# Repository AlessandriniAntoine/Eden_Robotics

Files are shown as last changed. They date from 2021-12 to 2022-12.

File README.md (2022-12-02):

# Eden_Robotics

Eden Robotics is a student project. The objective was to create a robotic arm capable of harvesting tomatoes. You can find a report [there](./Report/main.pdf).

<figure>
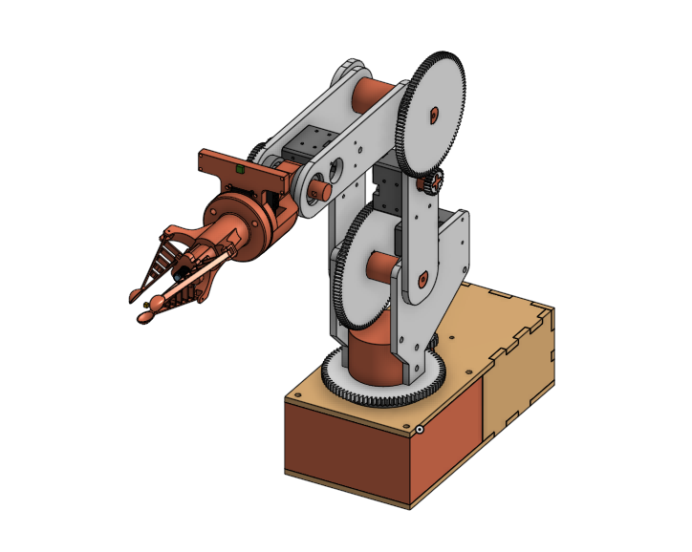
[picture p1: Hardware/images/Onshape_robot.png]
    
    <figcaption>Figure 1 : Robot Visualitaion</figcaption>
</figure>

<br/>
<br/>
<br/>

<figure>
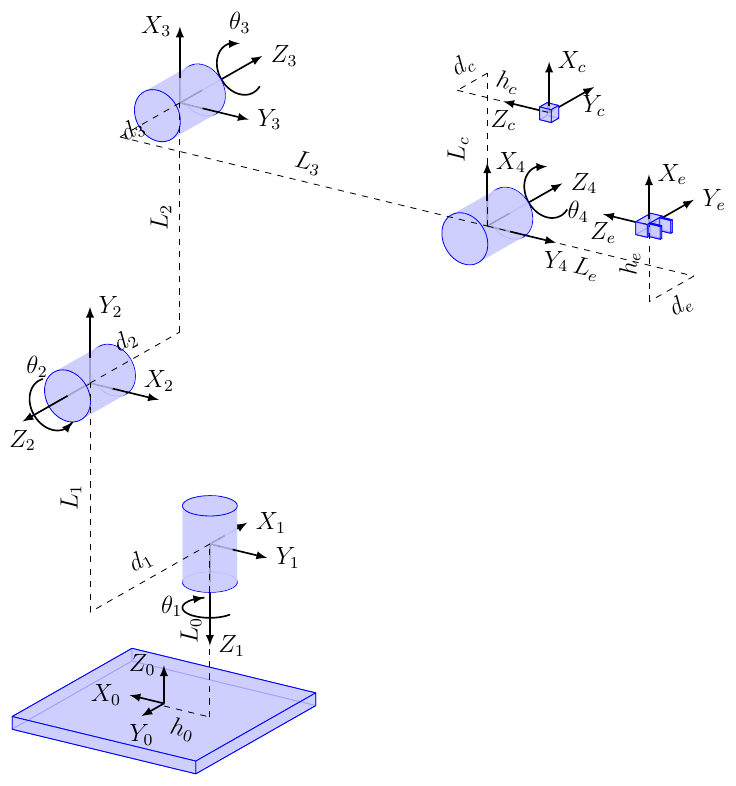
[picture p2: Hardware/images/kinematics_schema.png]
    
    <figcaption>Figure 2 : Kinematics schema</figcaption>
</figure>

## Hardware

We used the following hardware part :

- dynamixels motors and driver : U2D2, XL430,XC430, XM430,AX12W
- Raspberry pi 3
- USB camera

To construct the robot, the parts are in this [folder](./Hardware/stl). A notice can be found [there](./Hardware/Assembly_Plan.pdf). You can also found the Onshape model [here](https://cad.onshape.com/documents/8404446994fd5ae1242a5d56/w/0f8ef10f6026ba3e07bbdb54/e/7486e3cb0086b1a441d11061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).

We used Onshape to model the robot. Some rules, stated [here](./Hardware/README.md), must be respected during this creation. Thanks to this, a URDF model of the robot can be generated automatically (cf python part)

## Python

Each subfolder has a README file that explains more precisely how to use it.

### URDF

Using python, we transfer our Onshape model into an urdf model.

For more information see the [urdf_README](./Python/urdf/README.md).

### kinematics

Even if the inverse kinematics is done  in Matlab, some kinematics tools were done in python using modern_robotics library. Mainly because it facilitated the creation of node ROS and accelerated the process.

We used this library for :

- Forward kinematics
- compute configuration matrix of the end effector and the camera
- change point reference frame

For more information see the [kinematics_README](./Python/kinematics/README.md).

### Vision

Using openCV we have perfom :

- camera video display
- object tracking

For more information see the [vision_README](./Python/vision/README.md).

## Matlab

Thanks to the urdf file, it is possible to create a simscape multibody model of the robot.

Using matlab, we have perform:

- Forware kinematics
- Inverse kinematics
- closed loop model

For more information see the [matlab_README](./Matlab/README.md).

## Software

During the project, we used the following softwares :

- Matlab R2022a : ROS toolbox, Robotic system toolbox, simscape
- Python 3.8 : onshape-to-robot, modern robotics, openCV
- Ubuntu 20.04
- Onshape

## Useful links

- [eden_robotics_ros](https://github.com/AlessandriniAntoine/eden_robotics_ros.git) : branch ros1, package ros for this project
- [onshape-to-robot_documentation](https://onshape-to-robot.readthedocs.io/en/latest/)
- [modern_robotics_documentation](http://modernrobotics.org)
- [modern_robotics_github](https://github.com/NxRLab/ModernRobotics)

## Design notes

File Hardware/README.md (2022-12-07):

# Hardware

You can find the model here : [Onshape_model]([aa](https://cad.onshape.com/documents/8404446994fd5ae1242a5d56/w/0f8ef10f6026ba3e07bbdb54/e/7486e3cb0086b1a441d11061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)). You need an onshape acount to copy and modify it.

See the assembly instructions [here](./Assembly_Instructions.pdf)

## Design Rules

To keep a clean work environment, the following points should be respected:

- Name all parts with a specific name: it is the ID of the part and it has to be unique
- One subassembly by articulation: a subassembly contains all the parts of an articulation that have a fixed join between them
- One main assembly containing the motor links: the main assembly contains only the join that you want to see at the end. Usually, it is the dynamic join but it can be fixed to get a part separately.
- Assign material to each part: in Onshape, you precise the volumic mass, you need to pay attention in case you use PLA with a 3D printer. A part is never full at 100\% and you need to adapt the volumic mass to get the correct masS.
- Motor link in the main assembly needs to be named **dof_<link_name>**
- A relation between parent/child needs to be respected for every link: In Onshape, like all CAO software, there is a parent/child relation in every link. You really need to pay attention to this, it can be a source of many errors if you want to export your model. When you create a link, fixed or motorized, the first element you click on is the child. The second one is the father. You can then check the parent and the child as shown in the following image. It is therefore necessary to start from the origin to the end of the robot, respecting these relationships at the time of assembly.

### Parent Child

In Onshape, like all CAO software, there is a parent/child relation in every link. You really need to pay attention to this, it can be source of many errors if you want to export your model.

When you create a link, fixed or motorized, the first element you click on is the child. The second one is the father. You can then check the parent and the child as shown in the following image.

<center>
<figure>
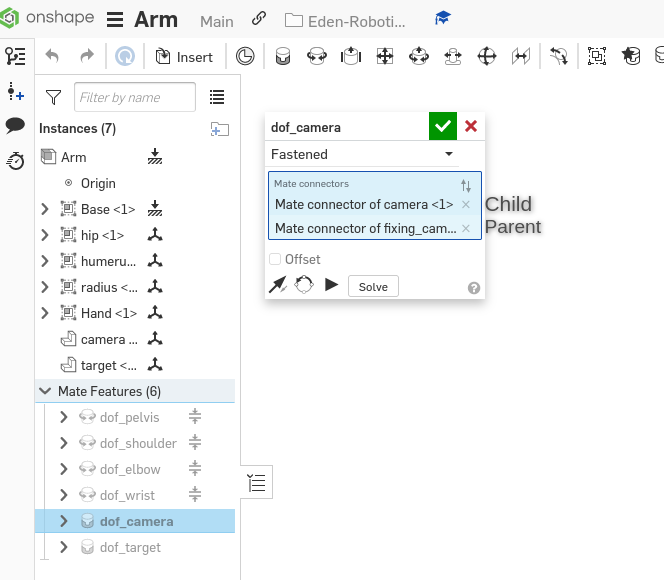
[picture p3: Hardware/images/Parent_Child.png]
    
    <figcaption>Figure 1: Parent Child relation Onshape</figcaption>
</figure>
</center>

## Kinematics

 A schema has been created thanks to sketck lib.
 
## Gmesh

This folder contains a try to create a tool to create easy stl shape from picture or drawing. However, it is still in progress.

## Useful links

- [sketch_lib_documentation](http://alexdu.github.io/sketch-lib/)

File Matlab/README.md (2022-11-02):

# Matlab

Create your simscape model using the urdf file :

```console
simimport(<urdf_path>)
```

Once it is done, you have a simulink file with a simscape model. You should run your file once. Then you can save the variables space that contains you robot. It will be useful for the inverse kinematics simulink block.

<center>
<figure>
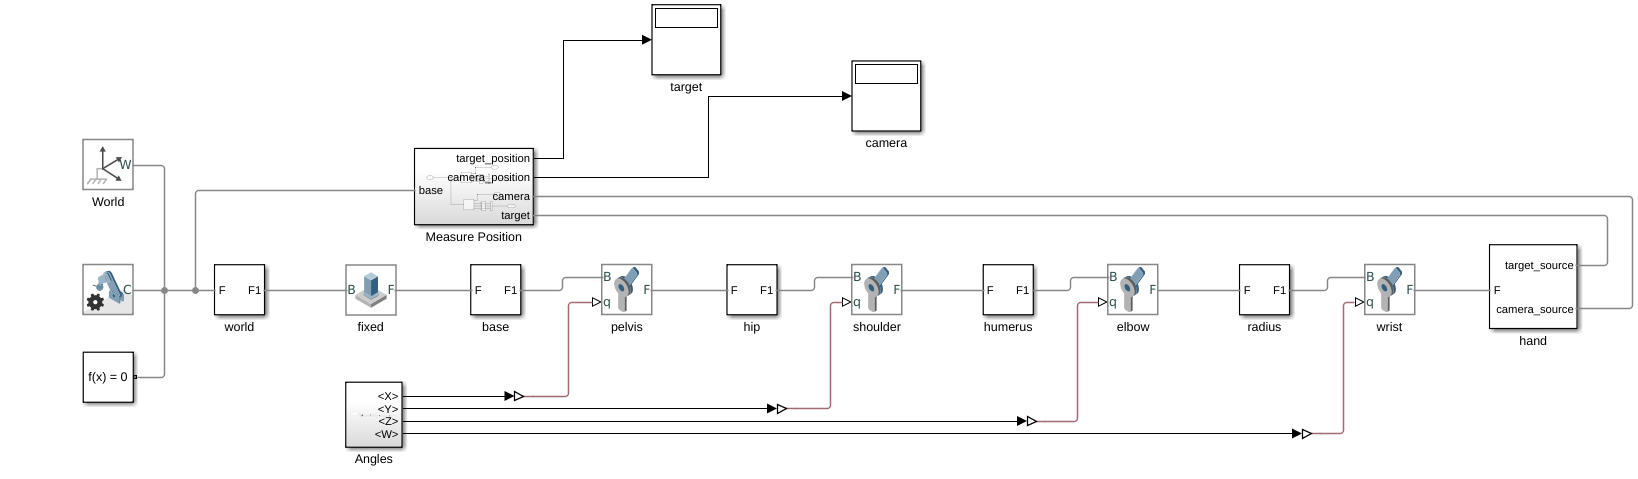
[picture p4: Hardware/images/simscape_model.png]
    
    <figcaption>Figure 1 : Simscape model</figcaption>
</figure>
</center>

Thanks to the different toolbox in matlab we perfom :

- inverse kinematics (inverse kinematics file)
- forward kinematics (robot file)
- closed loop model (closed loop)

<center>
<figure>
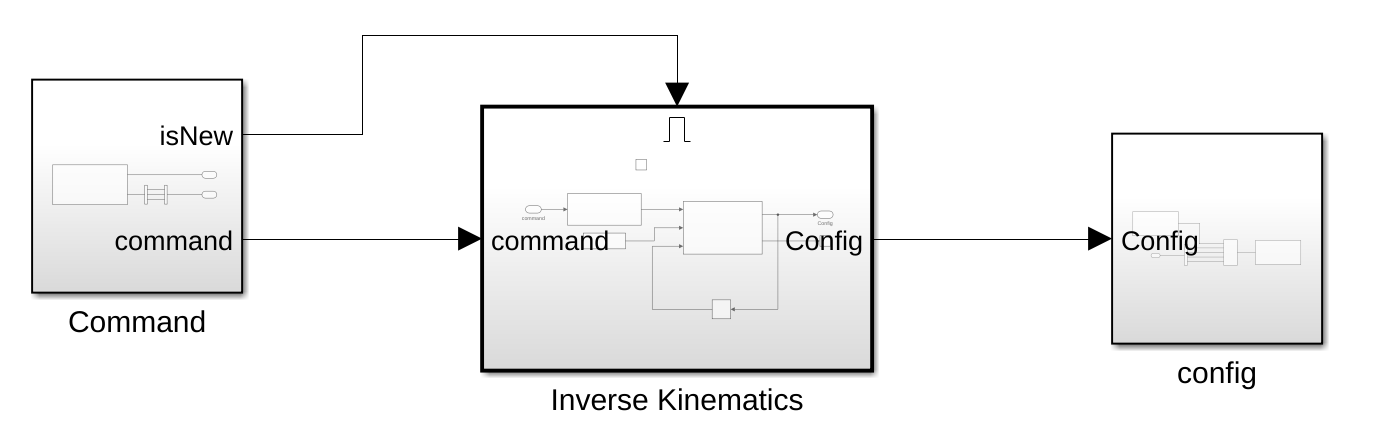
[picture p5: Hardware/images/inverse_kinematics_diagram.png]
    
    <figcaption>Figure 2 :Inverse kinematics diagram</figcaption>
</figure>
</center>

<center>
<figure>
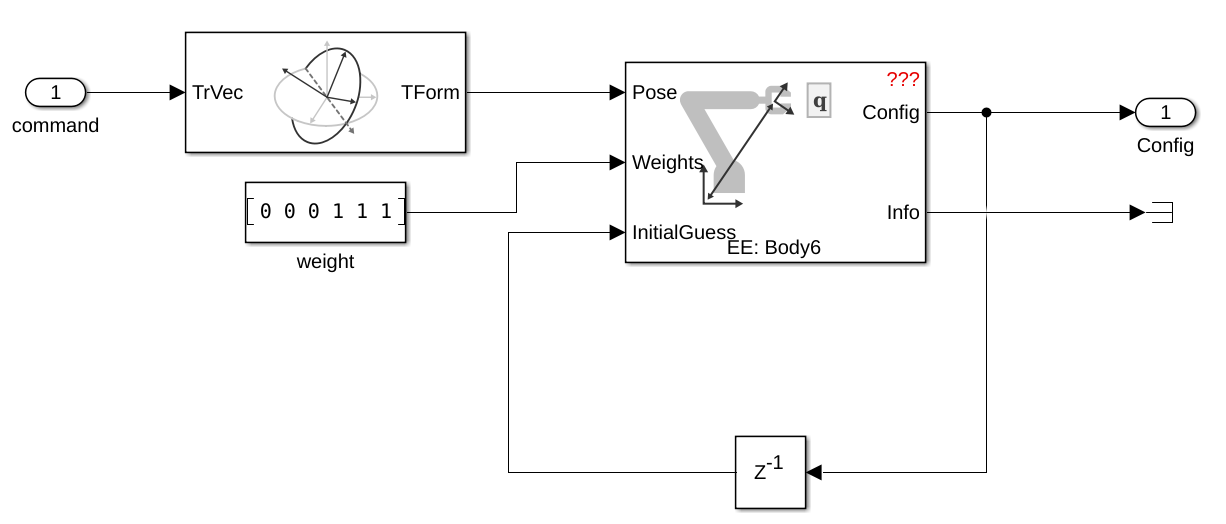
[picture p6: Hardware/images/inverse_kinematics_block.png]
    
    <figcaption>Figure 3 :Inverse kinematics block</figcaption>
</figure>
</center>

The files ForwarKinematics and position only send ros topic using knob. Thanks to that, you can modify easely a topic value to make some test for the forwark kinematics (joint values) or the inverse kinematics (target position).

## ROS

### Connect to ROS

To connect to ROS you will need to configure ROS Network Adress.You can access this in the **Simulation tab** by selecting **ROS Toolbox** > **ROS Network**. You will need to set :

- ROS Master
- Network Adress

To run files that contain ros block, you need a ROS master. You can either, run it on a terminal (recommended) with the following commande :

```console
~ $ source /opt/ros/noetic/setup.bash
~ $ roscore 
```

Or run in matlab terminal a **rosinit** command. Notice that if you do that, you cannot use the same ros master to run node that use not matlab.

### Generate Node

The ros folder contains files that are generated by Matlab to create ros packaga from a simulink file. To generate them you need set parameters. You can access this in the **modeling tab** > **Model Settings** > **Hardware Implementation** > **Hardware board settings** > **Target hardware resources** > **Groups** > **Build Options**. You need to set :

- Device Adress (127.0.0.1 if personnal)
- Username
- password
- Ros folder (already set)
- path to catkin workspace

Then you just have to generate the files. It will create :

- build_ros_model.sh
- <Simulink_file_name>.tgz

You can now create your package with the following command :

```console
~/Matlab_folder $ ./build_ros_model.sh <your_name>.tgz <path to catkin_workspace>
```

## Useful links

- [robotic_system_toolbox_documentation](https://in.mathworks.com/help/robotics/index.html?s_tid=CRUX_lftnav)
- [ros_toolbox_documentation](https://in.mathworks.com/help/ros/index.html?s_tid=CRUX_lftnav)
- [simscape_toolbox_documentation](https://in.mathworks.com/help/simscape/index.html)
- [simulink_documentaton](https://in.mathworks.com/help/simulink/index.html?searchHighlight=simulink&s_tid=srchtitle_simulink_1)
- [generate_node_simulink_tutorial](https://in.mathworks.com/help/ros/ug/generate-a-standalone-ros-node-from-simulink.html)

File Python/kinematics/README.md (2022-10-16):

# Kinematics

Despite the use of matlab for the kinematics of the robot, a part has also been developed under python to facilitate its use.

The kinematic diagram of the robot is as follows

<figure>
    
    <figcaption>Figure 1 : Kinematics schema</figcaption>
</figure>

The [parameters](./parameters.py) file contains all the variables and the initial configuration of the end effector and the camera. It contains the screw axis. All variables were measured in the state and the body frame.

The forward kinematics as been computed in both.

## Useful links

- [modern_robotics_documentation](http://modernrobotics.org)
- [modern_robotics_github](https://github.com/NxRLab/ModernRobotics)
- [modern_robotics_coding_manual](https://github.com/NxRLab/ModernRobotics/blob/master/doc/MRlib.pdf)
- [coursera_classes_modern_robotics](https://www.coursera.org/learn/modernrobotics-course1)

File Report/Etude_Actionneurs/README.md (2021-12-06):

### Dossier Matlab
Contient tous les éléments nécessaires à la simulation du robot sous simscape multibody.

Contient les fichiers matlab suivants : 
1. Bras_DataFile_PLA.m : correspond à tous les paramètres du bras (rotations, translations entre les parties 
2. Etude_PLA.m : Permet de simuler le bras et de récuper les couples, puissance et vitesse de rotation ainsi que de créer les graphiques correspondants 
3. Initilisation_PLA.m : A lancer en premier, permet de créer le robot nécessaire aux simulations 
4. Simulation_PLA.m : Contient les points d'arrivée et de départ et le temps de chaque simulation.

Contient les fichiers simulinks suivants : 
1. Bras_PLA.slx : modèle du bras avec des angles donnés 
2. Moteurs_PLA.slx : modèle de la simulation 

### Dossier Réducteur
1. Reducteur_PLA.m : Calcul le réducteur nécéssaire connaissant le couple nécéssaire et le couple moteur
2. Détermination réducteur.py : pareil
3. Vérification réducteur.py : renvoie les caractéristique nécéssaire du moteur connaissant celle nécéssaire et le réducteur

### Fichier PDF
Synthése pour chaque moteur des simulations puis du moteur choisis

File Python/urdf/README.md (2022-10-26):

# URDF

Once the Onshape model is created, having followed the rules stated in the [hardware_folder](../Hardware), you can export it to an urdf format.

As explain on the librairy documentation, you should create onshape API key. It is recommended to store them on your bashrc or zshrc because the secret key will no longer be shown.

```console
// Obtained at https://dev-portal.onshape.com/keys
export ONSHAPE_API=https://cad.onshape.com
export ONSHAPE_ACCESS_KEY=Your_Access_Key
export ONSHAPE_SECRET_KEY=Your_Secret_Key
```

Then, you should create a folder where you want your urdf file to be construct and write a config.json file:

```console
~ $ mkdir -p robot_urdf && touch robot_urdf/config.json
```

The config file must contain at least the following fields (see [config_file](./config.json) for this robot):

```console
{
    "documentId": "document-id",
    "assemblyName": "onshape assembly",
    "outputFormat": "urdf"
}
```

The document-id is the number (below XXXXXXXXX) you can find in Onshape URL:

```console
https://cad.onshape.com/documents/XXXXXXXXX/w/YYYYYYYY/e/ZZZZZZZZ
```

Once this is done, if you properly installed and setup your API key, just run:

```console
~ $ onshape-to-robot robot_urdf
```

If everything goes fine, an urdf file should have been created in the folder, the stl files have been downloaded and part file as well

## Useful Links

- [onshape-to-robot_documentation](https://onshape-to-robot.readthedocs.io/en/latest/)
- [urdf_tutorials](http://wiki.ros.org/urdf/Tutorials)

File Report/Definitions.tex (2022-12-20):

\def\MyClass{
Project Report
}

\def\MyTitle{
Eden Robotics
}

\def\MyAuthor{

\textit{Members:} \\
Antoine \textsc{Alessandrini}, Maxime \textsc{Bacquet}, Anna \textsc{Berger}, Héloïse \textsc{Boyer-Vidal}, Simon \textsc{Dahy}, Anna \textsc{Ducros}, Victor \textsc{Guinebertière}, Thomas \textsc{Jaouen}, David \textsc{Kirov}, Simon \textsc{Kurney}, Noé \textsc{Luxembourger}, Aya \textsc{Skhoun} 

\vspace{0.7cm}

\textit{Client:} \\
Mr. Patrick \textsc{Kedziora}

\vspace{0.7cm}

\textit{Coaches:} \\
Mr. Denis \textsc{LePicart}, Mr. Roland \textsc{Marcoin}

\vspace{0.7cm}

\textit{Consultants:} \\
Mr. Yannick \textsc{Dusch}, Mr. Alexandre \textsc{Kruszewski}, Mr. Denis \textsc{LePicart}

\vspace{0.7cm}

\textit{Date:} \\
September 2020 - February 2022

\vspace{0.7cm}

\textit{Written by:} \\
Antoine \textsc{Alessandrini}  \\

\def\MyAuthorShort{}
}

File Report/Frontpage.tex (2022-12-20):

\begin{titlepage}

\newcommand{\HRule}{\rule{\linewidth}{0.5mm}} 

\center 

\begin{figure}
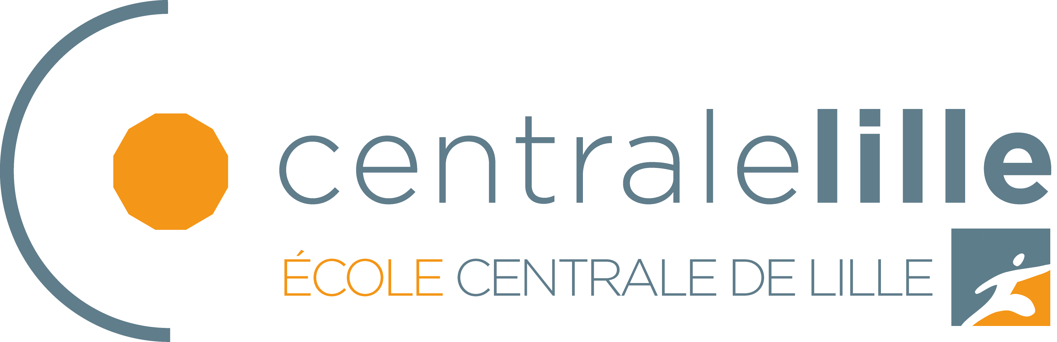
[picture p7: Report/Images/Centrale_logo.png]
\centerline{}
\end{figure}

\vspace{3.0cm}

%%%%%%%%%%%%%%%%%

\textsc{\Large \MyClass}\\ 

\vspace{0.5cm}

%%%%%%%%%%%%%%%%%%%%

\hrule
\vspace{0.4cm}
\hfill{\huge \bfseries \MyTitle}\hfill
\vspace{0.4cm}
\hrule

\vspace{1.5cm}

%%%%%%%%%%%%%%%%%%%
\MyAuthor

\vfill
\begin{figure}[H]
\centerline{}
\end{figure}

\vfill

\flushleft
Lille

\end{titlepage}

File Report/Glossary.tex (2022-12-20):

\makeglossaries

\newglossaryentry{CAD}
{
    name=CAD,
    description={the use of computers to aid in the creation, modification, analysis, or optimization of a design}
}

\newglossaryentry{disparity}
{
    name=disparity,
    description={The apparent motion of objects between a pair of stereo images}
}

\newglossaryentry{fk}
{
    name=forward kinematics,
    description={The use of a robot's kinematic equations to compute the end-effector's position from specified values for the joint parameters}
}

\newglossaryentry{frame}
{
    name=frame,
    description={An abstract coordinate system whose origin, orientation, and scale are specified by a set of reference points}
}

\newglossaryentry{gantt}
{
    name=Gantt diagram,
    description={Graphical representation of a schedule}
}

\newglossaryentry{hc}
{
    name=home configuration,
    description={Corresponds to the rest position, usually all joints or links are set to zero}
}

\newglossaryentry{hco}
{
    name=homogenous coordinates,
    description={$4\times1$ vector representing coordinates $x$, $[x 1]$}
}

\newglossaryentry{ik}
{
    name=inverse kinematics,
    description={The use of kinematic equations to determine a robot's motion (appropriate joints' configuration) to reach a desired position}
}

\newglossaryentry{kd}
{
    name=kinematic diagram,
    description={Illustates connectivity of links and joints of a mechanism}
}

\newglossaryentry{ms}
{
    name=market study,
    description={Analyze, understand, and measure the real functioning of the forces at work in a market}
}

\newglossaryentry{milestone}
{
    name=milestone,
    description={Siginificant stage or event in the development of something}
}

\newglossaryentry{mt}
{
    name=motor torque,
    description={The amount of rotational force that the motor develops}
}

\newglossaryentry{octopus}
{
    name=octopus diagram,
    description={Represents the relationship between a product and its environment}
}

\newglossaryentry{os}
{
    name=open-source software,
    description={A software with source code that anyone can inspect, modify, and enhance}
}

\newglossaryentry{payload}
{
    name=payload,
    description={Maximum mass a robot can support}
}

\newglossaryentry{redundancy}
{
    name=redundancy,
    description={The fact that a robot can reach a specified position with more than one joints configuration}
}

\newglossaryentry{ss}
{
    name=scope statement,
    description={Defines the purpose of the project, the stages of its realization, and the elements necessary to carry it out}
}

\newglossaryentry{sa}
{
    name=screw axis,
    description={Is used to describe rigid body motions and forces, be its axes of motion (such as the rotation axis of a pure rotation) or force (such as the line of action of a force)}
}

\newglossaryentry{servomotor}
{
    name=servomotor,
    description={A rotary or linear actuator that allows precise control of angular or linear position, velocity, and acceleration thanks to a position feedback sensor}
}

\newglossaryentry{step}
{
    name=step function,
    description={A discontinuous function, whose value is zero until x reaches a certain value t and a given value y when x is greater than t}
}

\newglossaryentry{sc}
{
    name=stereo camera,
    description={A camera with two or more lenses with a separate image sensor or film frame for each lens}
}

\newglossaryentry{tr}
{
    name=time response,
    description={Also called setting time, it is the time required for the response curve to reach and stay within a range of a certain percentage of the final value}
}

\newglossaryentry{tm}
{
    name=transformation matrix,
    description={Transforms one vector into another vector by the process of matrix multiplication The transformation matrix alters the cartesian system and maps the coordinates of the vector to the new coordinates}
}

\newglossaryentry{te}
{
    name=tunnel effect,
    description={case where the sponsor receives little or no information during implementation}
}

\newglossaryentry{wbs}
{
    name=WBS,
    description={Hierarchical breakdown of the necessary work}
}

\newglossaryentry{windup}
{
    name=windup,
    description={The situation in a PID feedback controller where a large change in setpoint occurs (say a positive change) and the integral term accumulates a significant error during the rise}
}

\newglossaryentry{workspace}
{
    name=Workspace,
    description={A specification of the reachable configuration of the end effector}
}

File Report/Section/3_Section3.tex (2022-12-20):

\section{Design}\insertloftspace
\setcounter{figure}{0}\setcounter{table}{0}
\label{Des}
\subsection{Brainstorming}
\label{BraSto}
Right after we defined the project, we took some time to propose ideas. The goal was to abstract from the existing and imagine different configurations, shapes, or mechanisms. So we made hand sketches to illustrate our different ideas as shown in the drawings below. 
\begin{figure}[H]
    \begin{subfigure}{.5\linewidth}
        \centering
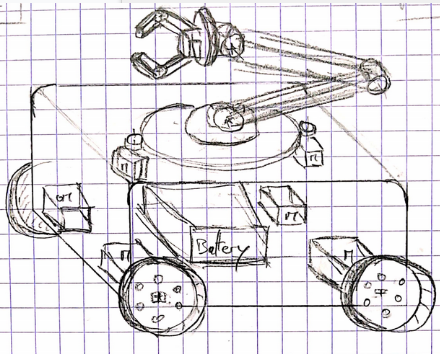
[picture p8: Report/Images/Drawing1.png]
        
        \caption{}
        \label{fig:Drawing1}
    \end{subfigure}%
    \begin{subfigure}{.5\linewidth}
        \centering
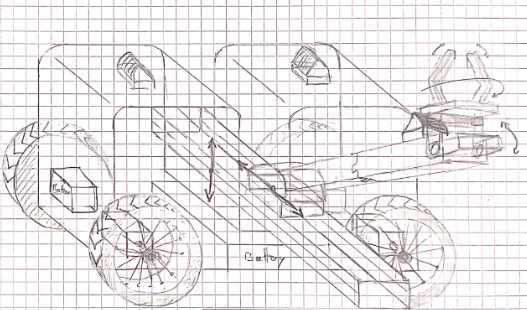
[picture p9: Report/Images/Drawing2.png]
        
        \caption{}
        \label{fig:Drawing2}
    \end{subfigure}\\[1ex]
    \begin{subfigure}{.5\linewidth}
        \centering
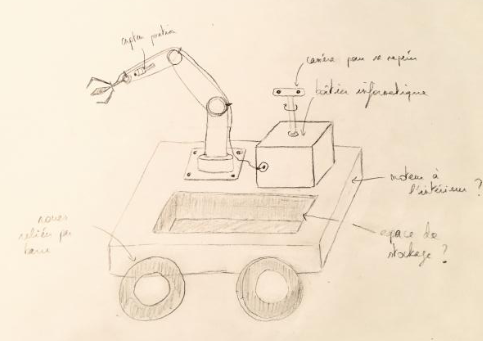
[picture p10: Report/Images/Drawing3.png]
        
        \caption{}
        \label{fig:Drawing3}
    \end{subfigure}
    \begin{subfigure}{.5\linewidth}
        \centering
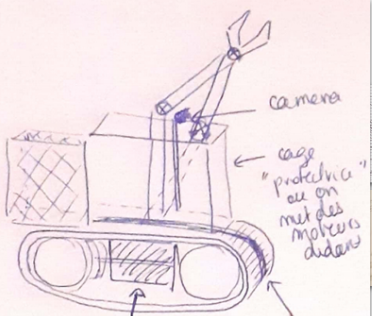
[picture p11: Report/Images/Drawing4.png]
        
        \caption{}
        \label{fig:Drawing4}
    \end{subfigure}
    \caption{Robot drawings}
    \label{fig:Drawings}
\end{figure}

In order to prototype and select a design quickly we also built two lego prototypes. This allowed us to define the basic design of the arm: a three-degree-of-freedom arm attached with a pivot link to the base. We hesitated with the design of the figure \ref{fig:Drawing2} with a central axis but when we built the lego prototype we found constraints too important to reach different points in space. In particular, the ability to work only in a 2D plane without moving the base.
\begin{figure}[H]
    \begin{subfigure}{.5\linewidth}
        \centering
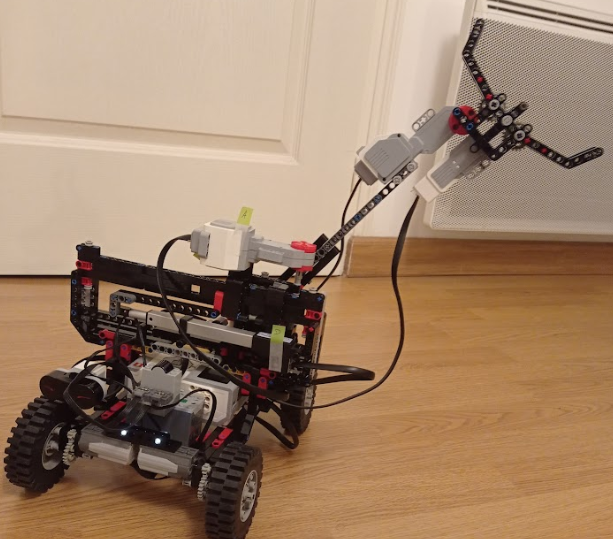
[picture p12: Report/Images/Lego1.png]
        
        \caption{}
        \label{fig:Lego1}
    \end{subfigure}%
    \begin{subfigure}{.5\linewidth}
        \centering
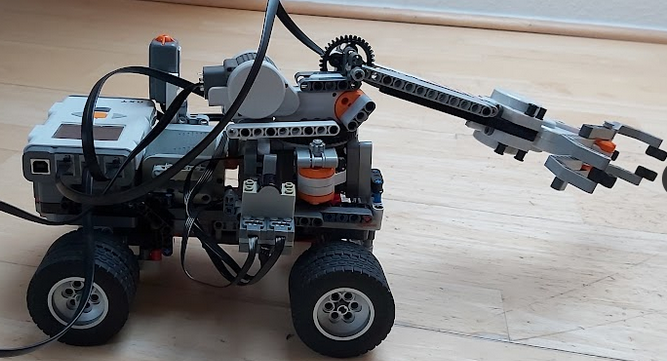
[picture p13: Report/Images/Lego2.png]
        
        \caption{}
        \label{fig:Lego2}
    \end{subfigure}\\[1ex]
    \caption{Lego robots}
    \label{fig:Legos}
\end{figure}

Like the market research and project definition, all members participated in this step in order to get as many ideas as possible but also to be sure everyone understand the future goal. We then divided ourselves into technical divisions as detailed in the previous \ref{Orga}. Once this process was finished, the mechanical pole could start a design in \gls{CAD}\footnote{the use of computers to aid in the creation, modification, analysis, or optimization of a design} using the software \textit{Onshape}.

\subsection{Onshape}
\label{Ons}
\subsubsection{Presentation}

To model our robot, we used the software \textit{Onshape} \cite{Onshape}. It is a computer-aided design software system, delivered over the Internet via a software-as-a-service model. This software offers many advantages : 
\begin{itemize}[noitemsep]
    \item collaborative
    \item quick to learn
    \item online
\end{itemize}

The last one may limit its use because it requires an internet connection.

\subsubsection{Rules}

Rules to standardize our work have also been established from the beginning. As we will see in the following parts, it is necessary to respect them to be able to exploit these documents with other software.
\begin{itemize}
    \item Name all parts with a specific name: it is the ID of the part and it has to be unique
    \item One subassembly by articulation: a subassembly contains all the parts of an articulation that have a fixed join between them
    \item One main assembly containing the motor links: the main assembly contains only the join that you want to see at the end. Usually, it is the dynamic join but it can be fixed to get a part separately.
    \item Assign material to each part: in \textit{Onshape}, you precise the volumic mass, you need to pay attention in case you use PLA with a 3D printer. A part is never full at 100\% and you need to adapt the volumic mass to get the correct masS.
    \item Motor link in the main assembly needs to be named \textit{dof\_\less link\_name\bg}
    \item A relation between parent/child needs to be respected for every link: In \textit{Onshape}, like all CAO software, there is a parent/child relation in every link. You need to pay attention to this, it can be a source of many errors if you want to export your model. When you create a link, fixed or motorized, the first element you click on is the child. The second one is the father. You can then check the parent and the child as shown in the following image. It is therefore necessary to start from the origin to the end of the robot, respecting these relationships at the time of assembly.
\end{itemize}
\begin{figure}[H]
    \centering
    
    \caption{Parent child principle}
    \label{fig:ParentChild}
\end{figure}

\subsection{Arm}
\label{Arm}
The design of the arm was done in 4 steps.

\subsubsection{Step 1}

For the first step, we looked for and bought an arm resembling the desired design. Thanks to this, the mechanical department was able to train on different tutorials and then to make an "easy" application that consisted only in reproducing this arm by respecting the rules stated. At the same time, the automatic pole was able to take advantage of this to make tests on a physical robot.
\begin{figure}[H]
    \begin{subfigure}{.5\linewidth}
        \centering
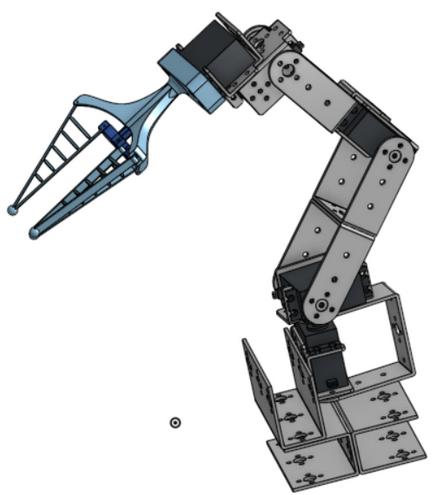
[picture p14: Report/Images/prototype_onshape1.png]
        
        \caption{Onshape design}
        \label{fig:Onshape1}
    \end{subfigure}%
    \begin{subfigure}{.5\linewidth}
        \centering
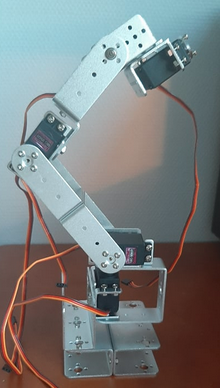
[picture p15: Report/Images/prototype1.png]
        
        \caption{Physical robot}
        \label{fig:Physical1}
    \end{subfigure}\\[1ex]
    \caption{Prototype 1}
    \label{fig:Prototype1}
\end{figure}

The purchase of this arm allowed a first quick design on which all the members could work. We thus avoided a waiting time for the computer science and automatic poles. They were able to work on this one and carry out various tests in order to leave time for the mechanical pole to create our own design that we were going to manufacture.

\subsubsection{Step 2 and 3}

In steps 2 and 3, we created different prototypes entirely on the computer. Little manufacturing was done, we only tested parts of the robot in order to save time and iterate as quickly as possible.
\begin{figure}[H]
    \begin{subfigure}{.5\linewidth}
        \centering
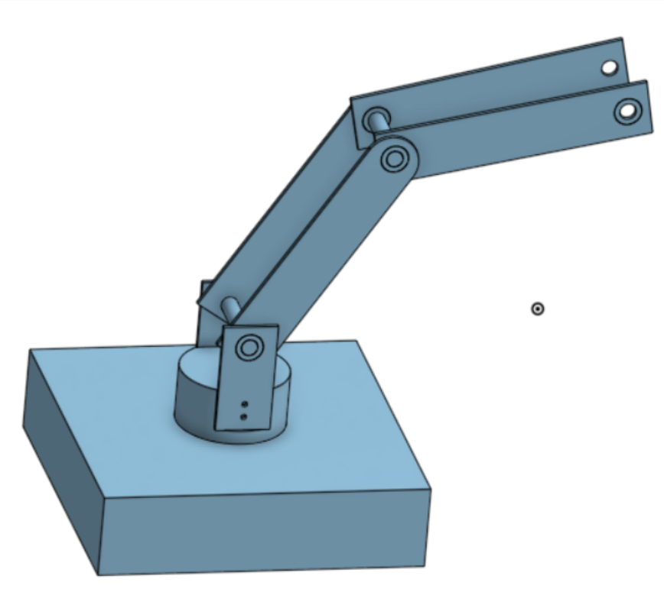
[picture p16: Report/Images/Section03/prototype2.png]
        
        \caption{Prototype 2}
        \label{fig:Prototype2}
    \end{subfigure}%
    \begin{subfigure}{.5\linewidth}
        \centering
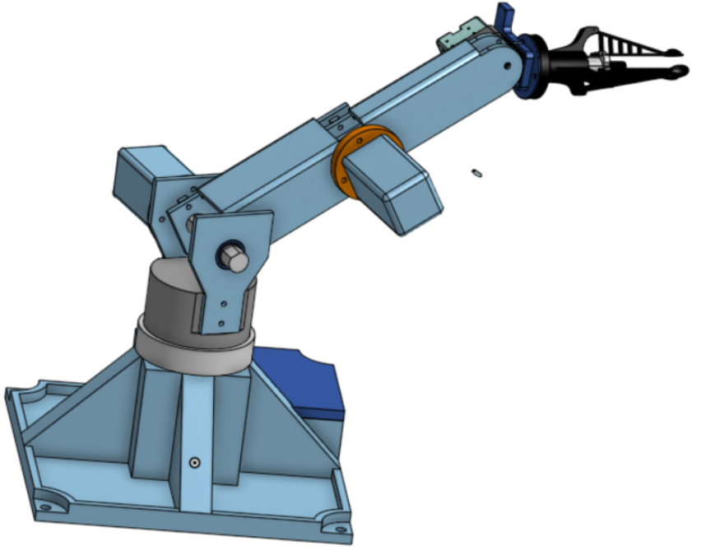
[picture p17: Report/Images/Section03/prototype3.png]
        
        \caption{Prototype 3}
        \label{fig:Prototype3}
    \end{subfigure}\\[1ex]
    \caption{Prototypes 2 and 3}
    \label{fig:Prototypes}
\end{figure}

Prototype 2 was a rough sketch of our robot. As we said, we decided to have 3 degrees of freedom on the arm (shoulder, elbow, wrist) and a pivot link on the base to reach a maximum of points in space. We can thus have a base that will settle in one place and an arm that will recover a maximum of tomatoes without having to move it. In view of the layout of the tomatoes, we also decided to have two parts that we will call humerus and radius almost the same size. 

\bigbreak
It allowed us to make choices like the types of joints, and the lengths of each of the parts. Some of us also followed the training courses offered by Centrale on 3D printing and laser cutting. Some parts of this design, although rough, have been created to practice.
\begin{figure}[H]
    \begin{subfigure}{.5\linewidth}
        \centering
        
        \caption{3D printed part}
        \label{fig:3D1}
    \end{subfigure}%
    \begin{subfigure}{.5\linewidth}
        \centering
        
        \caption{Laser cutting part}
        \label{fig:LC1}
    \end{subfigure}\\[1ex]
    \caption{3D printed and laser cutting examples}
    \label{fig:3DLC1}
\end{figure}

We then designed another robot (step 3) more complete since it integrates the wrist mechanism. The motors and the ball bearings were also represented, with realistic masses. Following the problems we noticed during the manufacturing of some parts, we also imagined a new structure for the arms to stiffen the whole. However, the geometry implied a one-piece construction of the arm rather than two laser-cut parts. It had to be 3D printed, which increased the production time. Although the structure was better bonded, these parts also lacked strength at the corners. It was therefore not retained.
\begin{figure}[H]
    \centering
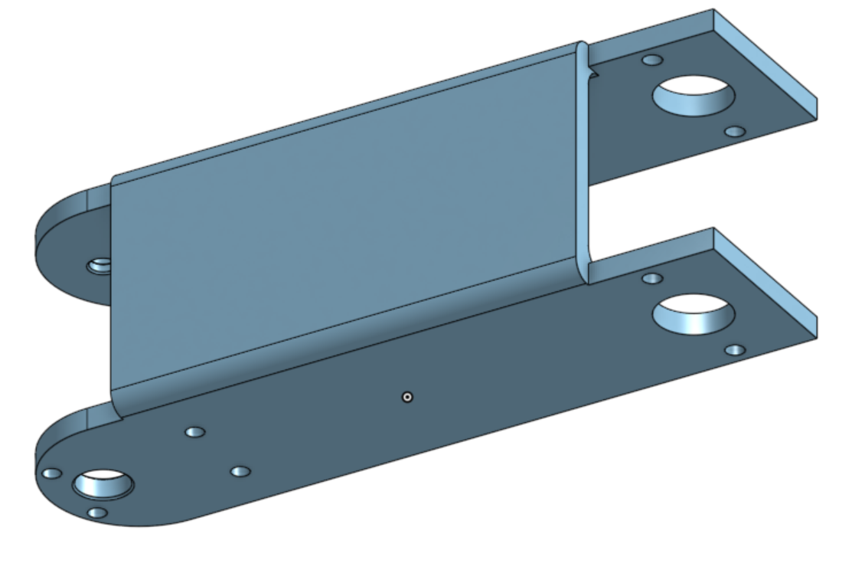
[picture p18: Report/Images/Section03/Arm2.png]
    
    \caption{Arm modified}
    \label{fig:Arm2}
\end{figure}

It is on this robot that the studies of part 6 were led first to select the motors for the final robot. 

\subsubsection{Step 4}

All these tests and changes lead us to step 4: the complete design of the robot and its complete fabrication. For this, we made some parts in PVC or plywood with a laser cut, we printed in 3D some parts. Others such as the filleted rods were directly purchased. To overcome the lack of rigidity, we added rods between the two plates of the humerus and radius. A building instruction to reproduce the robot can be found in appendix \ref{Instructions}. All the STL files can also be found on the GitHub page of this project.
\begin{figure}[H]
    \begin{subfigure}{.5\linewidth}
        \centering
        
        \caption{Partial assembly}
        \label{fig:PA}
    \end{subfigure}%
    \begin{subfigure}{.5\linewidth}
        \centering
        
        \caption{Final assembly}
        \label{fig:FA}
    \end{subfigure}\\[1ex]
    \caption{Arm step 4}
    \label{fig:AS4}
\end{figure}

This is only a prototype and improvements are still to be expected. We had some ideas that we, unfortunately, could not explore. Some PVC parts can be replaced by aluminum to increase the resistance, and a structure around the arm to manage the cables can also be added for example.

\subsection{Hand}
\label{Han}

The design of the hand was a crucial step. Based on what was being done and the advantages put forward, we created our own design. The two figures below present techniques to catch objects, one based on aspiration\cite{Abundant} and the other mimicking a human hand\cite{Prehenseur}. However, the first one is relatively complex and therefore expensive and long to implement. Moreover, there is a risk of damaging the fruit by sucking it too hard. The second one is not very adapted for tomatoes. 
\begin{figure}[H]
    \begin{subfigure}{.5\linewidth}
        \centering
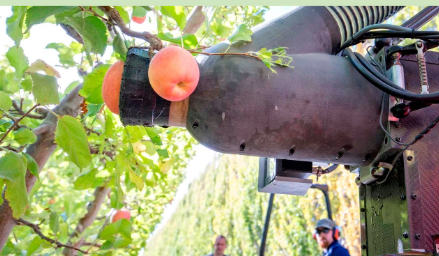
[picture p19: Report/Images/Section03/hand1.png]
        
        \caption{Hand 1}
        \label{fig:hand1}
    \end{subfigure}%
    \begin{subfigure}{.5\linewidth}
        \centering
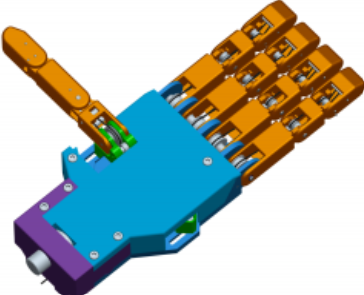
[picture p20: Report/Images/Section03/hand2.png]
        
        \caption{Hand 2}
        \label{fig:hand2}
    \end{subfigure}\\[1ex]
    \caption{Existing hands}
    \label{fig:ExistingHands}
\end{figure}

Our first idea was to create a hand composed of three deformable rights that would follow the shape of the tomato. These fingers are attached to a fixed part and to the same actuator to make them move at the same time. The actuator is a screw-nut system and an adapter to make the 3D-printed fingers move.
\begin{figure}[H]
    \begin{subfigure}{.5\linewidth}
        \centering
        
        \caption{Onshape design}
        \label{fig:HandProto1}
    \end{subfigure}%
    \begin{subfigure}{.5\linewidth}
        \centering
        
        \caption{Hand}
        \label{fig:HProtoReal1}
    \end{subfigure}\\[1ex]
    \begin{subfigure}{\linewidth}
        \centering
        
        \caption{Actuator system}
        \label{fig:HSystem}
    \end{subfigure}
    \caption{Hand V1}
    \label{fig:HandV1}
\end{figure}

Unfortunately, with our knowledge and facing the difficulty to find a material deformable enough to fit the shape of the tomato while supporting enough to pull it, we changed the shape of the fingers. While keeping the principle of three fingers, they have been adapted to have a spoon shape and come directly into the shape of the tomato.
\begin{figure}[H]
    \begin{subfigure}{.5\linewidth}
        \centering
        
        \caption{Hand picking tomato}
        \label{fig:HandPicking}
    \end{subfigure}%
    \begin{subfigure}{.5\linewidth}
        \centering
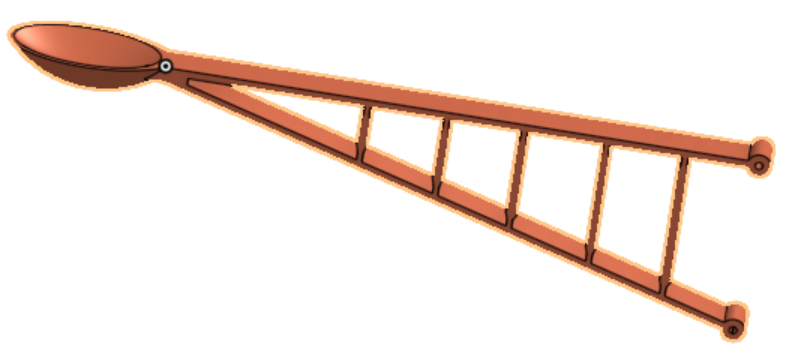
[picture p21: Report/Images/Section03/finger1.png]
        
        \caption{Finger}
        \label{fig:Finger}
    \end{subfigure}\\[1ex]
    \caption{Hand V2}
    \label{fig:HandV2}
\end{figure}

This requires greater precision when picking the fruit, however. This configuration also offers less flexibility when it comes to the different shapes of tomatoes. It could be interesting to try to pursue the principle of a deformable hand.

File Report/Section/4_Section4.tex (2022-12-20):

\section{Robot Characteristics}\insertloftspace
\setcounter{figure}{0}\setcounter{table}{0}

We indicate here the characteristics of the final robot but all these studies have been conducted on intermediate prototypes. They will be used in the following parts.

\subsection{Definition}

\textbf{Definition :} Given a vector $x=[x_1 x_2 x_3]^T \in \mathbb{R}^3$, we define : 
\begin{center}
    $[x] = \begin{bmatrix}
        0 & -x_3 & x_2 \\
        x_3 & 0 & -x_1 \\
        -x_2 & x_1 & 0 \\
    \end{bmatrix}$
\end{center}

\noindent\textbf{Definition :} Given two vectors $x$ and $y$ in $\mathbb{R}^3$, we define : $x\times y = [x]\cdot y$

\bigbreak
\noindent\textbf{Definition :} For a joint, we define the pitch $h = \frac{v}{w}$ with v: the linear speed and w the angular speed

\bigbreak
\noindent\textbf{Definition :} The screw is a $6\times1$ vector that represents the angular velocity when $\dot{\theta}=1$ and the linear velocity of the origin when $\dot{\theta}=1$. $S = \begin{bmatrix} s_w\\s_v\end{bmatrix}$ with $s_v = hw-s_w\times q$ where h is the pitch and q is a point on the axis of the screw.

\noindent\textbf{Definition :} For a given reference frame, a screw axis S is written as 
\begin{center}
    $S=\begin{bmatrix}
        s_w\\s_v
    \end{bmatrix}$
\end{center}
where either (i) $\|s_w\|$ = 1 or (ii) $\|s_w\|$ = 0 and $\|s_v\|$ = 1. If the pitch is finite ($h$ = 0 for a pure rotation), then $s_v = hs_w-s_w\times q$ where q is a point on the axis of the screw.

\subsection{Configuration}

\bigbreak
The figure below shows the \gls{kd}\footnote{Illustates connectivity of links and joints of a mechanism} of the robot. The figure defines an \{s\} \gls{frame}\footnote{An abstract coordinate system whose origin, orientation, and scale are specified by a set of reference points} at the bottom, an \{e\} frame at the end effector position, and a \{c\} frame at the camera position. The robot is at its \gls{hc}\footnote{Corresponds to the rest position, usually all joints or links are set to zero}. The joints are represented with the rotation (positive rotation about the axes is by the right-hand rule).

\bigbreak 
The parameters can be found with Onshape and are listed below: 

\begin{center}
    \fcolorbox{black}{white}{
        \begin{minipage}{0.8\linewidth}
            $L_0 = 0.069m$ \hspace{3cm} $d_0 = 0m$ \hfill $h_0 = 0.06m$ \\
            $L_1 = 0.116m$ \hspace{3cm} $d_1 = 0.018m$ \\ 
            $L_2 = 0.16m$ \hspace{3.2cm} $d_2 = 0.042m$ \\ 
            $L_3 = 0.155m$ \hspace{3cm} $d_3 = 0.01413m$ \\ 
            $L_c = 0.053m$ \hspace{3cm} $d_c = 0.0105m$ \hfill $h_c = 0.0815m$ \\
            $L_e = 0.2377m$ \hfill $d_e = 0.0105$ \hfill $h_e = 5.10^{-5}m$ \\
        \end{minipage}
    }
\end{center}

\begin{figure}[ht]
    \centering
    
    \caption{Kinematics schema}
    \label{fig:kinematicsSchema}
\end{figure}
\FloatBarrier

\bigbreak
We can then define $M_c$ and the $M_e$ \gls{tm}\footnote{Transforms one vector into another vector by the process of matrix multiplication The transformation matrix alters the cartesian system and maps the coordinates of the vector to the new coordinates} of the camera and the end effector from the base ($T_{sc}$ and $T_{se}$) when the robot is at its home configuration. 

\bigbreak
\begin{center}
    $
    M_c = \begin{bmatrix}
        0 & 0 & 1 & -h_0-L_3-h_c\\
        0 & -1 & 0 & d_1-d_2+d_3+d_c\\
        1 & 0 & 0 & l_0+l_1+l_2+l_c\\
        0 & 0 & 0 & 1
    \end{bmatrix}
    $
    and
    $
    M_e = \begin{bmatrix}
        0 & 0 & 1 & -h_0-L_3-h_c\\
        0 & -1 & 0 & d_1-d_2+d_3+d_c\\
        1 & 0 & 0 & l_0+l_1+l_2+l_c\\
        0 & 0 & 0 & 1
    \end{bmatrix}
    $
\end{center}

\subsubsection{Base frame}

In this subsection, we study the kinematics parameters in the base frame \{s\}. It will be the one used in the following sections.

\bigbreak
The rotation $S_{w_i}$ of each joint  in \{s\} are : 
\begin{center}
    $S_{w_1} = \begin{bmatrix} 0 \\ 0 \\ -1\end{bmatrix}$,
    $S_{w_2} = \begin{bmatrix} 0 \\ 1 \\ 0\end{bmatrix}$,
    $S_{w_3} = \begin{bmatrix} 0 \\ -1 \\ 0\end{bmatrix}$,
    $S_{w_4} = \begin{bmatrix} 0 \\ -1 \\ 0\end{bmatrix}$,
\end{center}

\bigbreak
We can also write the position of each joint  $q_1,q_2,q_3,q_4,q_c,q_e$ in \{s\}. Lining up the position as columns, we get : 

\begin{center}
    $
    \begin{bmatrix}
        -h_0 & -h_0 & -h_0 & -h_0-L_3 & -h_0-L_3-h_c & -h_0-L_3-L_e  \\
        0 & d_1 & d_1-d_2 & d_1-d_2+d_3 & d_1-d_2+d_3+d_c & d_1-d_2+d_3+d_e \\
        L_0 & L_0+L_1 & L_0+L_1+L_2 & L_0+L_1+L_2 & L_0+L_1+L_2+L_c & L_0+L_1+L_2+h_e \\
    \end{bmatrix}
    $
\end{center}

\bigbreak
There are all pure rotation joints, using the position, the rotation axis and the formula defined above we can calculate the \gls{sa}\footnote{Is used to describe rigid body motions and forces, be its axes of motion (such as the rotation axis of a pure rotation) or force (such as the line of action of a force)} $S_1,S_2,S_3,S_4$ in \{s\}. Lining up them as columns, we get : 

\begin{center}
    $S_{list} = 
    \begin{bmatrix}
        0 & 0 & 0 & 0 \\
        0 & 1 & -1 & -1 \\
        -1 & 0 & 0 & 0 \\
        0 & -L_0-L_1 & L_0+L_1+L_2 & L_0+L_1+L_2 \\
        -h_0 & 0 & 0 & 0 \\
        0 & -h_0 & h_0 & h_0+L_3
    \end{bmatrix}
    $
\end{center}

\subsubsection{End effector frame}

In this subsection, we study the kinematics parameters in the end effector frame \{e\}. However, it is not the one that will be used later. 

\bigbreak
The rotation axis $S_{w_i}$ of each joint  in \{e\} are : 
\begin{center}
    $S_{w_1} = \begin{bmatrix} -1 \\ 0 \\ 0\end{bmatrix}$,
    $S_{w_2} = \begin{bmatrix} 0 \\ -1 \\ 0\end{bmatrix}$,
    $S_{w_3} = \begin{bmatrix} 0 \\ 1 \\ 0\end{bmatrix}$,
    $S_{w_4} = \begin{bmatrix} 0 \\ 1 \\ 0\end{bmatrix}$,
\end{center}

\bigbreak
We can also write the position of each joint  $q_1,q_2,q_3,q_4,q_c,q_e$ in \{e\}. Lining up the position as columns, we get : 

\begin{center}
    $
    \begin{bmatrix}
        -h_e-L_2-L_1 & -h_e-L_2 & -h_e & -h_e & -h_e+L_c & 0  \\
        d_e+d_3-d_2+d_1 & d_e+d_3-d_2 & d_e+d_3 & d_e & d_e-d_c & 0 \\
        L_e+L_3 & L_e+L_3 & L_e+L_3 & L_e & L_e-h_c & 0 \\
    \end{bmatrix}
    $
\end{center}

\bigbreak
There are all pure rotation joints, using the position, the rotation axis and the formula defined above we can calculate the screw axis $B_1,B_2,B_3,B_4$ in \{e\}. Lining up them as columns, we get : 

\begin{center}
    $B_{list} = 
    \begin{bmatrix}
        -1 & 0 & 0 & 0 \\
        0 & -1 & 1 & 1 \\
        -1 & 0 & 0 & 0 \\
        0 & L_e+L_3 & -L_e-L_3 & -L_e \\
        -L_e-L_3 & 0 & 0 & 0 \\
        d_e+d_3-d_2+d_1 & h_e+L_2 & -h_e & -h_e
    \end{bmatrix}
    $
\end{center}

\subsection{Workspace}

In order to define our robot, we have determined the \gls{workspace}\footnote{A specification of the reachable configuration of the end effector}. To do this, we used the forward kinematic computed with python as explained in section 5. Knowing the limits of each link, we made loops to evaluate the reachable positions in the whole space. We then represented the working space according to the 3 planes of the robot: top, front, and side. Obviously, this does not allow us to visualize the complete workspace, but it is the clearest way to show it. However, our calculations allow us to access the full workspace, i.e. all the points reachable by the robot. We also put the python code to represent these figures. The robot is also present in the figures in red in its zero configuration to better estimate the working space. To understand how we compute the transformation matrix and the position see section 5.2.2.
\begin{figure}[H]
    \begin{subfigure}{.5\linewidth}
        \centering
        
        \caption{XY plan for z=0.07m}
        \label{fig:WorkspaceXY}
    \end{subfigure}%
    \begin{subfigure}{.5\linewidth}
        \centering
        
        \caption{XZ plan for y=0m}
        \label{fig:WorkspaceXZ}
    \end{subfigure}\\[1ex]
    \begin{subfigure}{\linewidth}
        \centering
        
        \caption{YZ plan for x=-0.06m}
        \label{fig:WorkspaceYZ}
        \end{subfigure}
        \caption{Workspace}
        \label{fig:Workspace}
\end{figure}
\FloatBarrier

\begin{minted}[linenos=true,bgcolor=LightYellow]{Python}
    # import kinematics parameters
    from parameters import * 
    import matplotlib.pyplot as plt
    # joint values in radian
    pelvis_limits = list(np.arange(-1.57,1.57,0.2))
    shoulder_limits = list(np.arange(-1.57,0.69,0.3))
    elbow_limits = list(np.arange(-1.57,1.05,0.4))
    wrist_limits = list(np.arange(0,1.57,0.4))
    # loop on values to get all positions
    x,y,z = [],[],[]
    for pelvis in pelvis_limits:
        for shoulder in shoulder_limits:
            for elbow in elbow_limits:
                for wrist in wrist_limits:
                    thetalist = np.array([pelvis,shoulder,elbow,wrist])
                    # compute transformation matrix and point
                    t = mr.FKinSpace(m_e,screw_list,thetalist)
                    p = t.dot(np.array([0,0,0,1]))[:-1]
                    x.append(p[0])
                    y.append(p[1])
                    z.append(p[2])
    # plot xy plan
    plt.axes()
    plt.plot(x,y,".b",ms = 3,alpha=0.3) # plot position
    plt.plot([p1[0],p2[0],pe[0]], [p1[1],0,pe[1]],"-r") # plot robot arm
    rectangle = plt.Rectangle((-0.12,-0.06), 0.24, 0.12, fc='red',ec="red") 
    plt.gca().add_patch(rectangle) # plot robot body
    plt.title('xy plan')
    plt.xlabel('x (m)')
    plt.ylabel('y (m)')
    \end{minted}

\subsection{Payload}

Another essential characteristic of our robot is the \gls{payload}\footnote{Maximum mass a robot can support before breaking}. A cherry tomato weighs on average 15g, so we need a robot able to lift at least 2 times that to avoid any problems. To measure the payload, we placed the robot in the "worst" configuration: arm stretched flat. We then measured the intensity of the shoulder motor to lift a given mass. Then we held the robot in position by blocking it and we operated the same motor by measuring the current at the moment of the break. For a DC motor, the current is proportional to the torque which is proportional to the mass, it is then possible to determine the maximum mass that the robot can support. 
\begin{figure}[H]
    \centering
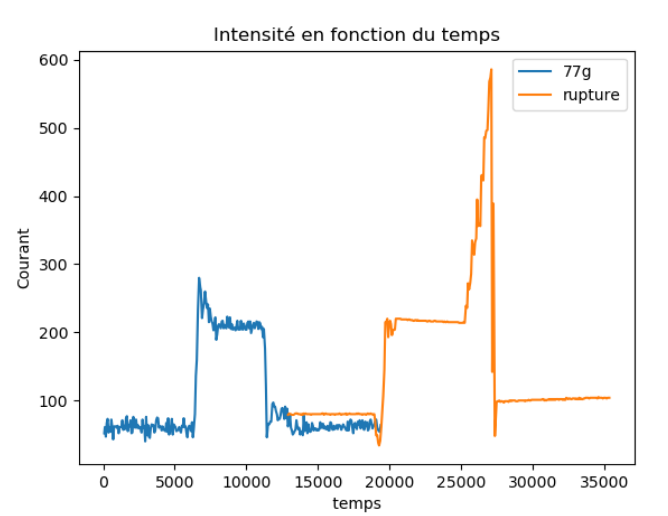
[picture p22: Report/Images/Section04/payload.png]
    
    \caption{Payload mesure}
    \label{fig:Payload}
\end{figure}
\FloatBarrier

The graph below shows the intensity in a specific unit of the motor. We measured an intensity of 300 for a mass of 77g and an intensity of 600 at breakage. Thus, \textbf{the payload of our robot is 144g}. We can note that this is not the limit of the robot. Indeed, it is the PVC gear that broke and not the physical limits of the robot. A stronger gear would allow for increasing the maximum mass if needed.

\subsection{Precision}

Finally, we have determined the accuracy of our robot. For this, we subjected our robot to a movement of 10cm from left to right several times. We made sure to mark our robot's trajectory and measured the distance covered. It was 12cm on average which makes a \textbf{accuracy of 2cm}. However, as we will see later, this is sufficient with the control method we have selected because the error is naturally compensated by the user.
\begin{figure}[ht]
    \centering
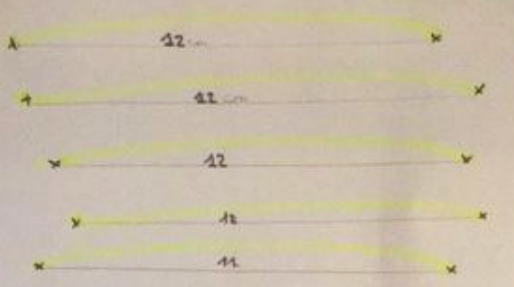
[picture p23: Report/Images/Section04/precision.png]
    
    \caption{Precision}
    \label{fig:Precision}
\end{figure}
\FloatBarrier

\subsection{Others}

We also have other characteristics that we have measured:
\begin{itemize}[noitemsep]
    \item height: 70cm including 50cm of arms
    \item mass: 2.7kg of which for 1.2kg the base
\end{itemize}

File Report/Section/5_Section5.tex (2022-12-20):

\section{Kinematics}\insertloftspace
\setcounter{figure}{0}\setcounter{table}{0}

In parallel to the design, we simulated the operation of the robot using \textit{Matlab}, \textit{Simulink}\cite{Matlab}, and python. The work explained from now on is done on the last prototype presented in the previous section. However, the principle applied has been the same throughout the project. The simultaneous work was important in order to anticipate the delays due to the manufacturing of the robot. The goal of this section is to compute the \gls{fk}\footnote{The use of the kinematic equations of a robot to compute the position of the end-effector from specified values for the joint parameters.} and the \gls{ik}\footnote{The use of kinematic equations to determine the motion (appropriate joints configuration) of a robot to reach a desired position.}.

\subsection{URDF Format}

The Universal Robot Description Format (URDF) is an XML (eXtensible Markup Language) file format used by the Robot Operating System (ROS) to describe the kinematics, inertial properties, and link geometry of robots. A URDF file describes the joints and links of a robot:

\begin{itemize}
    \item \textbf{Joints :} Joints connect two links: a parent link and a child link. A few of the possible joint types include prismatic, revolute (including joint limits), continuous (revolute without joint limits), and fixed (a virtual joint that does not permit any motion). Each joint has an origin frame that defines the position and orientation of the child link frame relative to the parent link frame when the joint variable is zero. The origin is on the joint's axis. Each joint has an axis 3-vector, a unit vector expressed in the child link's frame, in the direction of positive rotation for a revolute joint or positive translation for a prismatic joint.
    \item \textbf{Links :} While the joints fully describe the kinematics of a robot, the links define its mass properties. The elements of a link include its mass; an origin frame that defines the position and orientation of a frame at the link's center of mass relative to the link's joint frame described above; and an inertia matrix, relative to the link's center of mass frame, specified by the six elements on or above the diagonal. (Since the inertia matrix is symmetric, it is only necessary to define the terms on and above the diagonal.)
\end{itemize}

\bigbreak
This format will be useful to build the \textit{Simulink} model of the robot. Thankfully, the library \textbf{onshape-to-robot} in python can transform Onshape design into a URDF model. It is very important that you have respected the rules explained in the last section. It will download the STL file of each part and create all the joints and the links from the main assembly. The inertia matrices and the mass are also imported for each block. 

\bigbreak
As explained in the library documentation, you should create Onshape API key (see Onshape developer portal). It is recommended to store them on your bashrc or zshrc because the secret key will no longer be shown.

\bigbreak
\begin{center}
    \begin{minipage}{10cm}
        \fcolorbox{black}{Azure}{\parbox{\linewidth}{
            export ONSHAPE\_API=https://cad.onshape.com\\
            export ONSHAPE\_ACCESS\_KEY=Your\_Access\_Key\\
            export ONSHAPE\_SECRET\_KEY=Your\_Secret\_Key
        }}
    \end{minipage}
\end{center}

\bigbreak
Then, you should create a folder where you want your URDF file to be constructed and write a config.json file:
\begin{commandshell}
    mkdir -p robot\_urdf && touch robot\_urdf/config.json
\end{commandshell} 

\bigbreak
The config file must contain at least the following fields :
\begin{center}
    \begin{minipage}{8cm}
        \fcolorbox{black}{Azure}{\parbox{\linewidth}{
            \{\\
                \hspace*{0.8cm}"documentId": "document-id",\\
                \hspace*{0.8cm}"assemblyName": "onshape assembly",\\
                \hspace*{0.8cm}"outputFormat": "urdf"\\
            \}
        }}
    \end{minipage}
\end{center}

The documentId is the number (below XXXXXXXXX) you can find in Onshape URL:
\\https://cad.onshape.com/documents/XXXXXXXXX/w/YYYYYYYY/e/ZZZZZZZZ.

\bigbreak
Once this is done, if you properly installed and set up your API key, just run the following command. It will create a URDF file and put the STL file in the folder.
\begin{commandshell}
    onshape-to-robot robot_urdf
\end{commandshell} 

\bigbreak
The file will contain only the joints define in the final assembly. This is why you need subassemblies with fixed parts. As we can see in the extract below, the camera has a fixed joint with the hand. Also, it downloads all STL files and describes the visual position of each. However, it has only one global parameter for each subassembly that define the inertia.

\begin{figure}[ht]
    \centering
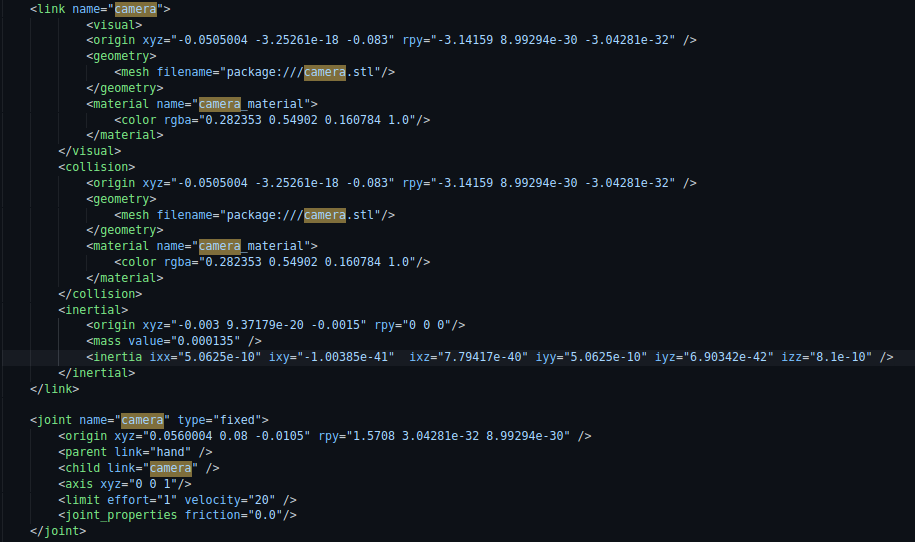
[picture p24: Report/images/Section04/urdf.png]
    
    \caption{URDF file extract}
    \label{fig:URDFextract}
\end{figure}
\FloatBarrier

\subsection{Forward kinematics}

To calculate the forward kinematics of our arm we used two different methods. This allowed us to compare the results and validate them. 

\subsubsection{Matlab simulation}

To begin with, \textit{Matlab} offers the possibility to import a URDF file describing a robot to make a \textit{Simulink} model using the simscape toolbox. This is the easiest method when you have the URDF file. It also has the advantage of visually simulating the robot. Indeed, the model is based on the STL files of each part. To create the model, simply run the following command in \textit{Matlab} : 
\begin{minted}[linenos=true,bgcolor=matlabColor]{matlab}
    %% create robot model from urdf
    smimport(<path to urdf>)
\end{minted}

\bigbreak
It will open a \textit{Simulink} file, once it is created, the joints must be modified so that the motor torque is calculated automatically and the desired angles can be entered manually. Finally, a position sensor linking the reference frame and the target frame must be added. We can then obtain the position of the hand for a given angle vector. 

\bigbreak
\begin{figure}[ht]
    \centering
    
    \caption{Simulink model}
    \label{fig:Simulink}
\end{figure}
\FloatBarrier

\bigbreak
\begin{figure}[ht]
    \centering
    
    \caption{Matlab robot visualization}
    \label{fig:MatlabRobot}
\end{figure}
\FloatBarrier

\bigbreak
It should be noted that a target block positioned at the center of the fingers has been added in the Onshape model. It is in a fixed link with the hand and this link is defined in the general assembly. Thus, when creating the URDF file, this target appears separately. It allows having an easy way to locate it. The mass of this object, which must be defined, is $10^{-5}$ to be considered as zero. The same thing has been done for the camera position. 

\subsubsection{Python simulation}

\textbf{Definition :} Let $S = (w,v)$ be a screw axis. If $\|w\|=1$ then, for any distance $\theta\in\mathbb{R}$ traveled along the axis,
\begin{center}
    $e^{[S]\theta}=
    \begin{bmatrix}
        e^{[w]\theta} & (I\theta+(1-\cos\theta)[w]+(\theta-sin\theta)[w]^2)v\\
        0 & 1
    \end{bmatrix}$
\end{center}
If w=0 and $\|v\|=1$ then 
\begin{center}
    $e^{[S]\theta}=\begin{bmatrix}
        I & v\theta\\
        0 & 1
    \end{bmatrix}$
\end{center}

\bigbreak
The second approach is more theoretical and is based on the kinematic parameters seen previously. To realize the calculations we used the python library modern robotics \cite{Mordern_Robotic}. It has native functions to calculate the forward kinematics. We will explain here how it computes the position of the end effector from the joints' position. Then we show how to use it in real life.

\bigbreak
This library is based on the exponentials of matrices to calculate the position of the end effector from the coordinates of each link. It uses the following formula: 

\begin{center}
    $T(\theta) = e^{[S_1]\theta_1}e^{[S_2]\theta_2}e^{[S_3]\theta_3}e^{[S_4]\theta_4}M$    
\end{center}
where $\theta$ is a $4\times1$ vector of joint coordinates, $S_i$ is the screw axes of the joint i and M is the transformation matrix when the robot is at its zero configuration.

\bigbreak
So we can use the function FKinSpace which takes as arguments M,$\theta$, and $S_{list}$ as defined above. Depending on whether we want the position of the camera or the end effector, we just have to change the M matrix. This method was faster to perform the calculations and faster to test a large number of values. However, it does not allow visualization.

\begin{minted}[linenos=true,bgcolor=LightYellow]{Python}
# import kinematics parameters
from parameters import * 
import modern_robotics as mr
# define desired angles 
thetalist = np.array([0,0,0,0])
# get transformation matrix and extract the position
t = mr.FKinSpace(m_e,screw_list,thetalist)
p = t.dot(np.array([0,0,0,1]))[:-1]
\end{minted}

\bigbreak
For the same set of angles, we then obtain the following results using \textit{Matlab} and python: 
\begin{table}[ht]
    \centering
    \begin{tabular}{|p{4cm} | p{4.5cm} | p{4.5cm}|} 
        \hline
        \textbf{joints (rad)} & \textbf{Matlab position (m)} & \textbf{Python Position (m)}\\ [0.3ex] 
        \hline\
        [0 0 0 0] & [-0.4527 0.00063 0.3455] & [-0.4527 0.00063 0.3455] \\ 
        \hline
        [pi/4,-pi/3,0,pi/3] & [-0.1286 0.06948 0.07537] & [-0.1286  0.06949 -0.07533] \\ 
        \hline
        [pi/4,pi/6,-pi/6,pi/3]& [-0.2259 0.1668 0.4583] & [-0.2258  0.1667  0.4583] \\ 
        \hline
    \end{tabular}
    \caption{Matlab and Python result for forward kinematics}
\end{table}

\bigbreak
As we can see, the results are identical at $10^{-4}m$. We can therefore validate the kinematic model of our robot. The position of \textit{Matlab} is correct since it comes from an explicit model and allows visualization.

\subsection{Inverse kinematics}

In the same way, we used two methods to calculate the inverse kinematics. The objective is to determine the coordinates of each link from a given position.

\subsubsection{Matlab simulation}

Once we had a \textit{Simulink} model, we were able to create a \textit{Matlab} variable that represents the robot. It is obtained with the script below.  This variable contains information about each link (position, parent, child) but also about each body (mass, center of mass, and inertia). The bodies are numbered from 1 to 7. The number 1 corresponds to the base and 7 to the end effector. We could identify them from the information on mass and inertia.

\begin{minted}[linenos=true,bgcolor=matlabColor]{matlab}
%% create robot matrix
open_system('robot.slx')
S=sim('robot.slx')
[robot,importInfo] = importrobot(gcs)
robot.DataFormat = 'column';
\end{minted}

\bigbreak
The Robotic System toolbox then allows calculating the inverse kinematics. Indeed, there is a block \textit{inverse kinematics} which takes as input the desired configuration (transformation matrix), weights which allow adjusting the importance of reaching the desired orientation and translation according to the 3 axes and returns the list of the position of each link. This block takes as a parameter the robot variable created before. You must then indicate the name of the body corresponding to the end effector.

\bigbreak
The block also offers the possibility to choose the resolution method. We have selected the Levenber-Marquardt method leaving the original resolution parameters. This method requires providing an initial guess if possible close to the real value. As we will explain in the following parts, our robot will always start in the same position: the zero configuration. We, therefore, provided this angle vector as an origin.

\bigbreak
\begin{figure}[ht]
    \centering
    
    \caption{Inverse kinematics simulink}
    \label{fig:InverseKinSimulink}
\end{figure}
\FloatBarrier

\bigbreak
We are only interested in the position of the hand. Indeed, the hand being symmetrical the orientation of the fingers to catch objects is not important. Thus, the weights for the orientation are null and the ones for the position are at the maximum.

\bigbreak
To verify the validity of the method, we retrieved the values of the link coordinates found by this block for desired end effector positions. Then, we submitted the robot in forward kinematics to these angles and verified that the positions are the same. Even if we know a set of angles corresponding to this position, depending on the initial hypothesis, the angles found can be different. Thus, comparing the value of the angles is not a good way to make sure that the resolution is working properly. As we do not take into account the orientation, we have only compared the positions.

\begin{table}[ht]
    \centering
    \begin{tabular}{|p{4.5cm} | p{4.5cm} | p{5cm}|} 
        \hline
        \textbf{desired position (m)} & \textbf{real position (m)} & \textbf{angles (rad)}\\ [0.3ex] 
        \hline\
        [-0.4527 0.00063 0.3455] & [-0.4542 0.00063 0.3455] & [$9.10^{-6}$ $9.10^{-3}$ $9.10^{-3}$ 0] \\ 
        \hline
        [-0.1286 0.06948 0.07537] & [-0.1288 0.06968 0.0739] & [0.7854  0.6981 0.7006 1.377] \\ 
        \hline
        [-0.2259 0.1668 0.4583] & [-0.2269 0.1678 0.4585] & [0.7855  0.6981  -0.1312 0.6766] \\ 
        \hline
    \end{tabular}
    \caption{Inverse kinematics results with Matlab}
\end{table}
\FloatBarrier

\bigbreak
In the case of the table above, the initial assumption is always [0 0 0 0]. The desired position and the actual position are identical at $10^{-3}m$. We can therefore validate the model. Nevertheless, the closer the initial value is to the final result, the smaller the error is. As we will see later, in our case, the arm will start in its zero configuration. We, therefore, know the value of these angles. In order to be as accurate as possible, this will be our starting point for calculating the inverse kinematics in all cases. As we can see from the table, this is sufficient to obtain a satisfactory result in all cases.

\subsubsection{Python simulation}

To perform the inverse kinematics with python, we relied again on the library \textit{modern robotic}. Inverting the kinematic forward matrix may not be impossible in some cases (\gls{redundancy}\footnote{The fact that a robot can reach a specified position with more than one joints configuration} for example), so it is necessary to start from an initial guess and then iteratively calculate the result. It is based on the Newton-Raphson method to compute the solution. 

\bigbreak
\textbf{Newton-Raphson method :} To solve the equation $g(\theta)=0$ numerically for a given differentiable function $g:\mathbb{R}\rightarrow\mathbb{R}$, assume $\theta^0$ is an initial guess for the solution. Write Taylor's expansion of $g(\theta)$ at $\theta^0$ and truncate it at first order. Keeping only these terms, set $g(\theta)=0$ and solve for $\theta$. Using this value of $\theta$ as the new guess for the solution and repeating the above, we get the following iteration : 
\begin{center}
    $g(\theta) = g(\theta^0)+\displaystyle{\frac{\partial g}{\partial\theta}(\theta^0)(\theta-\theta^0)}$\\
    $\theta = \theta^0-\displaystyle{(\frac{\partial g}{\partial\theta}(\theta^0))^{-1}g(\theta^0)}$\\
    $\theta^{k+1} = \theta^k-\displaystyle{(\frac{\partial g}{\partial\theta}(\theta^k))^{-1}g(\theta^k)}$
\end{center}
 This iteration is repeated until some stopping criterion is satisfied: $|g(\theta^k)-g(\theta^{k+1}|/|g(\theta^k)|\leq\epsilon$ for some user-prescribed threshold value $\epsilon$.
 
 \bigbreak
 If we apply this to our case, we call $f$ the forward kinematics function: $f(\theta) = x$. We define J the jacobian of $f$, $J(\theta^k)= \displaystyle{\frac{\partial f}{\partial\theta}|_{\theta^k}}$ and $\Delta\theta = \theta^{k+1}-\theta^k$. Using the Newton-Raphson method on the problem : $f(\theta)=x_d$, we will solve $f(\theta)-x_d=0$ :
 \begin{center}
     $x_d-f(\theta^k)=J(\theta^k)\Delta\theta$
 \end{center}
 Depending on the fact that J is invertible, we will invert it or use the pseudo inverse to solve it. 
 
 \bigbreak
 All this algorithm is already implemented in the \textit{modern robotic} library. To compute the inverse kinematics in the base frame we need to specify: The joint screws S expressed in the base frame, the end effector home configuration M, the desired end effector configuration T, an initial guess $\theta^0$ and the tolerances $e_\omega$ and $e_\upsilon$ on the final error.
 \begin{center}
     [$\theta$,success] = IKinSpace(S,M,T,$\theta^0$,$e_\omega$,$e_\upsilon$)
 \end{center}
 
 As we explained for \textit{Matlab}, we are only interested in the final position of the end effector. So we put a large value for $e_\omega$ (1) the orientation error and a very small value for $e_\upsilon$ (0.005) the position error.
 
 \bigbreak
 Unfortunately, we didn't have enough time to develop this part and we never managed to make the solutions converge. However, with a little more time, using python would speed up the development of the software by avoiding the use of \textit{Matlab} and the code generator.

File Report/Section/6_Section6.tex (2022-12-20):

\section{Torque Study}\insertloftspace
\setcounter{figure}{0}\setcounter{table}{0}

\subsection{General principal}

As soon as we were able to create the first model, we were interested in the necessary \gls{mt}\footnote{The amount of rotational force that the motor develops}. The objective was to determine the characteristics of each joint. Even if it was not the final robot, the different prototypes allowed us to have an estimation that we updated as soon as a choice was made. 

\bigbreak
In order to determine the necessary motors, we measured the following variables:
\begin{multicols}{3}
    \begin{itemize}[noitemsep]
        \item torque
        \item rotation speed
        \item power
    \end{itemize}
\end{multicols}

\bigbreak
\begin{figure}[ht]
    \centering
    
    \caption{Joint sensing block}
    \label{fig:SensingBlock}
\end{figure}
\FloatBarrier

\bigbreak
All these measurements were made in simulation with \textit{Matlab}. In the simscape model, we can modify the linkage blocks to return the torque and rotational speed. The Power is measured by multiplying the two. The units are not specified and depend on the units defined in the URDF file. In our case : 
\begin{multicols}{2}
    \begin{itemize}[noitemsep]
        \item length: m
        \item time: s
        \item mass: kg
        \item angle: rad
        \item force: N
        \item power: W
    \end{itemize}
\end{multicols}

We remind the relationship between torque, speed, and power: 
\begin{center}
    $P\hspace{0.3cm}=\hspace{0.3cm}CW$ with $P$ in $W$, $C$ in $N.m$, and $W$ in $rad.s^{-1}$
\end{center}

\bigbreak
To make these measurements, we built the following model: a block to send a trajectory, a block for inverse kinematics, and a block of simulation on which we come to carry out the measurements. It was important not to control the position of the links directly to avoid any discontinuity. Indeed, it is necessary that all the functions are derivable twice as a function of time to calculate the torque and the speed of rotation. This is why we make our robot follow a given trajectory.
\begin{figure}[ht]
    \centering
    
    \caption{Joint analysis model}
    \label{fig:JointGlobalModel}
\end{figure}
\FloatBarrier

\begin{figure}[ht]
    \centering
    
    \caption{Joint analysis robot measure}
    \label{fig:JointRobotModel}
\end{figure}
\FloatBarrier

\bigbreak
We develop in the following sub-sections the results for each link. After having estimated the characteristics a margin of 30\% was taken. Our consultant explained to us that it was a security. 

\bigbreak
In reality, only the power delivered interested us to select the engines. Indeed, if an engine is able to provide a certain power, we must look at the tuple (torque, speed) allowing this power. If one of the two does not meet the necessary values, a gear can be added. Let's take a gear of speed $r$, $\omega'= r\omega$ and $C'= \frac{C}{r}$ or $P'= \omega'C'=r\omega\frac{C}{r} = \omega C = P$. The gear allows changing the torque and the speed without modifying the power. Therefore, a corresponding gear must exist.

\bigbreak
A static study was also conducted. We placed the robot in the "worst" configuration for each link and then we measured the torque required to maintain the robot in this position. The torques indicated on the motors' data sheet do not usually guarantee a static hold. To make sure that our motors are powerful enough, we multiplied this value by 3 to choose them. 

\bigbreak
The table below lists the characteristics required for each linkage as well as the estimates obtained on the first prototype. It is important to note that this one, although farther from reality, is still close. Moreover, the final values are all lower because we have reduced the mass of the robot. In order to anticipate the delivery time, we based ourselves on results obtained on intermediate prototypes. We can then validate this method. 

\begin{table}[ht]
    \centering
    \begin{tabular}{|p{1.5cm} | p{4cm} | p{4cm}|p{5cm} |} 
        \hline
        \textbf{Joint} & \textbf{Power/estimate (W)} & \textbf{Torque/estimate (N)}& \textbf{Angulare speed/estimate (rad/s)}\\ [0.3ex] 
        \hline\
        Pelvis & 0.2/1 & 0.2/4.2 & 0.9/0.23 \\ 
        \hline
        Shoulder & 1.8/4 & 5.4/9.8 & 0.77/0.4 \\ 
        \hline
        Elbow & 0.7/2.3 & 2.07/2.4 & 0.78/0.94 \\ 
        \hline
        Wrist & 0.23/0.4 & 0.38/1.1 & 0.94/0.35 \\ 
        \hline
    \end{tabular}
    \caption{Power, torque, and speed rotation needed per joint}
\end{table}
\FloatBarrier

\subsection{Static}

For the static study, we put the robot in the position that requires the most effort to hold it in place. It is thus in a horizontal position with its arm stretched out. This is indeed the position where the torque is the most important for the shoulder, the elbow, and the wrist. In the static position, there is never any effort on the pelvis.
\begin{figure}[ht]
    \centering
    
    \caption{Static position}
    \label{fig:StaticPosition}
\end{figure}
\FloatBarrier

\bigbreak
We obtain the following results. We have plotted in blue the measured value and in red the value that our motor must be able to provide to ensure that it will be able to maintain this position. The torques indicated on the data sheets are generally dynamic torques and not static. According to the advice given to us, we take three times the value obtained in static to be sure the motor will be able to give enough torque.
\begin{figure}[ht]
    \centering
    
    \caption{Static torque}
    \label{fig:StaticTorque}
\end{figure}
\FloatBarrier

\bigbreak
These values could have been calculated manually. ONSHAPE allows finding the mass and the position of the center of gravity for a given set of parts. Thus, by retrieving the mass and the distance between the center of gravity and the link, we could have calculated the torque by assimilating the set of selected parts to a point of mass $m$ at a distance $d$ from the link.
\begin{center}
    $C\hspace*{0.3cm}=\hspace*{0.3cm}m*g*d$
\end{center}
\begin{table}[ht]
    \centering
    \begin{tabular}{|p{1.5cm} | p{2cm} | p{2.5cm}| p{2.7cm} | p{2.7cm} |} 
        \hline
        \textbf{Joint} & \textbf{Mass (kg)} & \textbf{Distance (m)}& \textbf{Torque (N.m)}& \textbf{Matlab (N.m)}\\ [0.3ex] 
        \hline
        Shoulder & 0.852 & 0.222 & 1.8 & 1.8 \\ 
        \hline
        Elbow & 0.460 & 0.152 & 0.68 & 0.68 \\ 
        \hline
        Wrist & 0.165 & 0.78 & 0.13 & 0.13 \\ 
        \hline
    \end{tabular}
    \caption{Static torque}
\end{table}
\FloatBarrier

\bigbreak
It can be noted that the values calculated and measured via \textit{Matlab} are almost identical. This also allows us to validate our measurement model and to make sure that we can rely on the values found with the simulation to choose the motors.

\subsection{Joint movement}

For each of the links, we conjectured the most "difficult" trajectory to achieve. We then tested it as well as different trajectories to make sure that we were right. The duration was also chosen according to the amplitude of the movement in order to meet the speed criterion defined in the specifications. We present here only the trajectory having presented the highest values. A margin of 30 \% was then retained following the advice of our consultant to take into account the frictions as well as the possible differences between the simulation and the reality.

\subsubsection{Pelvis}

In the case of the pelvis, the motor needs the most power when the arm is stretched horizontally and rotates around the base. So we made the robot make a half circle in 2s to measure the torque, the power, and the rotation speed.
\begin{figure}[ht]
    \centering
    
    \caption{Pelvis trajectory seen from top}
    \label{fig:PelvisTrajectory}
\end{figure}
\FloatBarrier

\bigbreak
As we can see on the graph below, in this case, the maximum power is $0.15W$. For this power, the torque is $0.16N.m$ and the rotation speed is $0.95rad.s^{-1}$. By adding 30\% we obtain a power of $0.2W$ and a torque of $0.21N.m$. The torque being superior to the one found to maintain the arm in static, finding a motor capable of delivering such power will be sufficient.
\begin{figure}[ht]
    \centering
    
    \caption{Pelvis characteristics}
    \label{fig:PelvisCharacteristics}
\end{figure}
\FloatBarrier

\subsubsection{Shoulder}

In the case of the shoulder, the motor needs the most power when the arm starts stretched horizontally and rises only around this axis. So we made the robot make a quarter circle in 2s to measure the torque, the power, and the rotation speed.
\begin{figure}[ht]
    \centering
    
    \caption{Shoulder trajectory seen from side}
    \label{fig:ShoulderTrajectory}
\end{figure}
\FloatBarrier

\bigbreak
As we can see on the graph below, in this case, the maximum power is $1.41W$. For this power, the torque is $1.83N.m$ and the rotation speed is $0.77rad.s^{-1}$. By adding 30\% we obtain a power of $1.83W$ and a torque of $2.34N.m$. The torque found is lower than the one needed to keep the robot static, so care must be taken to deliver both the power and the torque needed.
\begin{figure}[ht]
    \centering
    
    \caption{Shoulder characteristics}
    \label{fig:ShoulderCharacteristics}
\end{figure}
\FloatBarrier

\subsubsection{Elbow}

In the case of the elbow, the motor needs the most power when the arm starts at 90 degrees at this link and rotates to a horizontal position. So we made the robot make a quarter circle in 2s to measure the torque, the power, and the rotation speed.

\begin{figure}[ht]
    \centering
    
    \caption{Elbow trajectory}
    \label{fig:ElbowTrajectory}
\end{figure}
\FloatBarrier

As we can see on the graph below, in this case, the maximum power is $0.51W$. For this power, the torque is $0.66N.m$ and the rotation speed is $0.77rad.s^{-1}$. By adding 30\% we obtain a power of $0.67W$ and a torque of $0.86N.m$. The torque found is lower than the one needed to keep the robot static, so care must be taken to deliver both the power and the torque needed.
\begin{figure}[ht]
    \centering
    
    \caption{Elbow characteristics}
    \label{fig:ElbowCharacteristics}
\end{figure}
\FloatBarrier

\subsubsection{Wrist}

In the case of the wrist, the motor needs the most power when the arm starts at 45 degrees at this link and rotates around. So we made the robot make a quarter circle in 2s to measure the torque, the power, and the rotation speed.

\begin{figure}[ht]
    \centering
    
    \caption{Wrist trajectory}
    \label{fig:WristTrajectory}
\end{figure}
\FloatBarrier

As we can see on the graph below, in this case, the maximum power is $0.18W$. For this power, the torque is $0.19N.m$ and the rotation speed is $0.94rad.s^{-1}$. By adding 30\% we obtain a power of $0.23W$ and a torque of $0.24N.m$. The torque found is lower than the one needed to keep the robot static, so care must be taken to deliver both the power and the torque needed.
\begin{figure}[ht]
    \centering
    
    \caption{Wrist characteristics}
    \label{fig:WristCharacteristics}
\end{figure}
\FloatBarrier

\subsection{Hardware choices}

Just as we presented the results on the final robot for the torque, we also continue here. So the gears we will calculate will not be the ones we have mounted on the robot because we had based ourselves on the intermediate model. To speed up the manufacturing of the robot, we decided to buy \gls{servomotor}\textcolor{SteelBlue}{s}\footnote{A rotary or linear actuator that allows precise control of angular or linear position, velocity, and acceleration thanks to a position feedback sensor} so that we don't have to do any electronics. Dynamixel \cite{Dynamixel} motors were thus recommended. First, because they are widely used in robotics and very reliable but also because a ROS package has already been created with many examples to integrate them very quickly into our software. We have only selected the motors provided by this company by respecting two criteria: a reasonable price and the necessary characteristics respected by adding a gear if necessary.

\begin{figure}[ht]
    \centering
    
    \caption{Dynamixel servomotor principle}
    \label{fig:DynamixelPrinciple}
\end{figure}
\FloatBarrier

\subsubsection{Pelvis}

In view of the different models available at dynamixel, we have selected the following engine: \textbf{dynamixel XL430-W250}. The following graph shows the performance of the motor. In particular, in black, the maximum torque that can be delivered according to the speed of rotation of the motor. By multiplying the two we obtain the maximum power.
\begin{figure}[ht]
    \centering
    
    \caption{Pelvis motor performance}
    \label{fig:PelvisMotor}
\end{figure}
\FloatBarrier

\bigbreak
The necessary characteristics measured at the time as well as the one measured with the last version and the one of the engine are summarized below.
\begin{table}[ht]
    \centering
    \begin{tabular}{|p{1.5cm} | p{2cm} | p{2.5cm}| p{2.7cm} | p{2.7cm} |} 
        \hline
        \textbf{Joint}& \textbf{Power (W)} & \textbf{Torque (N.m)} & \textbf{Angular Speed (rad/s)} & \textbf{Static torque (N.m)}\\ [0.3ex]
        \hline
        previous need & 1 & 4.2 & 0.1 & 0 \\ 
        \hline
        actual need & 0.2 & 0.2 & 0.9 & 1.4 \\ 
        \hline
        motor & 0.65 & 0.73 & 0.9 & 1.5\\ 
        \hline
    \end{tabular}
    \caption{Pelvis motor specification}
\end{table}
\FloatBarrier
The motor is able to deliver directly the necessary dynamic and static values. No gearbox is really necessary. However, at the time we made the measurements, because of a more approximate model and our less good mastery of \textit{Matlab}, we had found much higher values. So we calculated that we needed a gear with a ratio of 1/7.

\subsubsection{Shoulder}

 We have selected the following engine: \textbf{dynamixel XM430-W350}. The following graph shows the performance of the motor. In particular, in black, the maximum torque that can be delivered according to the speed of rotation of the motor. By multiplying the two we obtain the maximum power.
\begin{figure}[ht]
    \centering
    
    \caption{Shoulder motor performance}
    \label{fig:ShoulderMotor}
\end{figure}
\FloatBarrier

\bigbreak
The necessary characteristics measured at the time as well as the ones measured with the last version and the one of the engine are summarized below.
\begin{table}[ht]
    \centering
    \begin{tabular}{|p{1.5cm} | p{2cm} | p{2.5cm}| p{2.7cm} | p{2.7cm} |} 
        \hline
        \textbf{Joint}& \textbf{Power (W)} & \textbf{Torque (N.m)} & \textbf{Angular Speed (rad/s)} & \textbf{Static torque (N.m)}\\ [0.3ex]
        \hline
        previous need & 2.8 & 7.6 & 0.4 & 5.2 \\ 
        \hline
        actual need & 1.8 & 2.4 & 0.77 & 5.1 \\ 
        \hline
        motor & 2.3 & 2.87 & 0.83 & 4.1\\ 
        \hline
    \end{tabular}
    \caption{Shoulder motor specification}
\end{table}
\FloatBarrier
The motor is able to deliver directly the necessary dynamic values. However, the static torque is not sufficient and a gearbox will then be necessary with a ratio $r=\frac{4.1}{5.1}=1.3$. At the time we made the measurements, we had found higher values. So we calculated that we needed a gear with a ratio of 1/4.8.

\bigbreak
After mounting the robot, we measured the percentage of the maximum torque used by the motor to make the same trajectory. We realized that we are not even using 10\% of the maximum value. This confirms that the simulation results on the last prototype are much closer to reality and that we could replace the present gears.

\subsubsection{Elbow}

 We have selected the following engine: \textbf{dynamixel XC430-W150}. The following graph shows the performance of the motor. In particular, in black, the maximum torque that can be delivered according to the speed of rotation of the motor. By multiplying the two we obtain the maximum power.
\begin{figure}[ht]
    \centering
    
    \caption{Elbow motor performance}
    \label{fig:ElbowMotor}
\end{figure}
\FloatBarrier

\bigbreak
The necessary characteristics measured at the time as well as the ones measured with the last version and the one of the engine are summarized below.
\begin{table}[ht]
    \centering
    \begin{tabular}{|p{1.5cm} | p{2cm} | p{2.5cm}| p{2.7cm} | p{2.7cm} |} 
        \hline
        \textbf{Joint}& \textbf{Power (W)} & \textbf{Torque (N.m)} & \textbf{Angular Speed (rad/s)} & \textbf{Static torque (N.m)}\\ [0.3ex]
        \hline
        previous need & 2.26 & 2.4 & 1 & 1.86 \\ 
        \hline
        actual need & 0.7 & 0.86 & 0.78 & 2.07 \\ 
        \hline
        motor & 1.2 & 0.7 & 0.83 & 1.6\\ 
        \hline
    \end{tabular}
    \caption{Elbow motor specification}
\end{table}
\FloatBarrier
The motor is able to deliver directly the necessary dynamic power. However, the static and dynamic torques are not sufficient and a gearbox will then be necessary with a ratio $r=\frac{2.07}{1.6}=1.3$. The dynamic torque needs a ratio of $r=\frac{0.86}{0.7}=1.23$, a ratio of 1.3 is then perfect. At the time we made the measurements, we had found higher values. So we calculated that we needed a gear with a ratio of 1/5.

\bigbreak
After mounting the robot, we measured the percentage of the maximum torque used by the motor to make the same trajectory. We realized that we are not even using 20\% of the maximum value. This confirms that the simulation results on the last prototype are much closer to reality and that we could replace the present gears.

\subsubsection{Wrist}

In view of the different models available at dynamixel, we have selected the following engine: \textbf{dynamixel XL430-W250}. The following graph shows the performance of the motor. In particular, in black, the maximum torque that can be delivered according to the speed of rotation of the motor. By multiplying the two we obtain the maximum power.
\begin{figure}[ht]
    \centering
    
    \caption{Wrist motor performance}
    \label{fig:WristMotor}
\end{figure}
\FloatBarrier

\bigbreak
The necessary characteristics measured at the time as well as the ones measured with the last version and the one of the engine are summarized below.
\begin{table}[ht]
    \centering
    \begin{tabular}{|p{1.5cm} | p{2cm} | p{2.5cm}| p{2.7cm} | p{2.7cm} |} 
        \hline
        \textbf{Joint}& \textbf{Power (W)} & \textbf{Torque (N.m)} & \textbf{Angular Speed (rad/s)} & \textbf{Static torque (N.m)}\\ [0.3ex]
        \hline
        previous need & 0.36 & 1.04 & 0.35 & 0 \\ 
        \hline
        actual need & 0.23 & 0.24 & 0.95 & 0.38 \\ 
        \hline
        motor & 0.65 & 0.73 & 0.9 & 1.5\\ 
        \hline
    \end{tabular}
    \caption{Wrist motor specification}
\end{table}
\FloatBarrier
The motor is able to deliver directly the necessary dynamic and static values. No gearbox is really necessary. However, at the time we made the measurements, because of a more approximate model and our less good mastery of \textit{Matlab}, we had found much higher values. So we calculated that we needed a gear with a ratio of 1/2.2.

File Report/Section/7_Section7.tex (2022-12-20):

\section{Joystick Control}\insertloftspace
\setcounter{figure}{0}\setcounter{table}{0}

\subsection{Principle}

The initial request of our customer was a remote-controlled arm. This was the easiest and fastest solution to implement. Mr. Kedziora also wanted to avoid using artificial intelligence in order not to lengthen the prototype manufacturing time. Despite our fears about the difficulties that this type of order can pose, he really insisted that we use this method, which is the first one that we have put in place.

\bigbreak
In this configuration, a camera, fixed on the arm at the level of the hand, allows the user to have a video return. An Xbox controller in our case is used to control the arm. The commands sent by the user are done in the camera's frame.
\begin{figure}[H]
    \begin{subfigure}{.5\linewidth}
        \centering
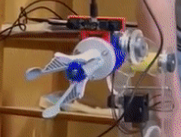
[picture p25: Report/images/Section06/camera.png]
        
        \caption{Position}
        \label{fig:CameraRobot}
    \end{subfigure}%
    \begin{subfigure}{.5\linewidth}
        \centering
        
        \caption{View}
        \label{fig:CameraView}
    \end{subfigure}\\[1ex]
    \caption{Camera}
    \label{fig:Camera}
\end{figure}
\FloatBarrier

\bigbreak
The control of the three axes in the camera frame is done with the two joysticks on the controller. The left joystick allows to move according to the plane (x,y) of the camera (see \ref{fig:kinematicsSchema} and the right joystick manages the depth. This movement is then transformed into a command to move along the desired axis. Some features listed below have also been added to the buttons to facilitate the work of the user and the proper functioning of the arm.
\begin{itemize}[noitemsep]
    \item authorize the movement: button A
    \item prohibit the movement: button B
    \item return to zero position : button X
    \item return to deposit position : button Y
\end{itemize}

\begin{figure}[ht]
    \centering
    
    \caption{Xbox Controller}
    \label{fig:XboxController}
\end{figure}
\FloatBarrier

\bigbreak
As explained in the previous section, the inverse kinematics calculates the necessary angles for a given position in the base frame \{s\}. However, it seemed more natural to us to make the user work in the camera reference frame \{c\} and then to change the reference frame. For this, we reused the modern robotics library. In the same way that we can calculate the transformation matrix between the base and the end effector from the position of the links, we can calculate the one between the base and the camera. 
\begin{center}
    $T_{sc} =\displaystyle \prod_{n=1}^4e^{[S_i]\theta_i}M_c$
\end{center}

\bigbreak
Then the relation between the position in the reference frame and the position in the reference frame is the following:
\begin{center}
    $p_s = T_{sc}p_c$
\end{center}

\bigbreak
Attention, $T_{sc}$ being a 4x4 matrix, $p_s$ and $p_c$ are \gls{hco}\footnote{$4\times1$ vector representing coordinates $x$, $[x 1]$}:$p = [p\hspace{0.2cm}1]$. At each command sent by the user, we retrieve the position of each of the links and then we apply the following code that puts into practice the previous equations. We obtain the position in the base frame.

\bigbreak
\begin{minted}[linenos=true,bgcolor=LightYellow]{Python}
    # import kinematics parameters
    from parameters import * 
    import modern_robotics as mr
    # receive angles and desired position from ros 
    thetalist = get_angles()
    p_c = get_position()
    p_c = np.array([p_c 1])
    # get transformation matrix and change the position
    t = mr.FKinSpace(m_c,screw_list,thetalist)
    p_s = np.dot(t,p_c)
    p_s = p[:3]
\end{minted}

\bigbreak
The instruction sent by the user is added to an offset. Indeed, we want to control the position of the center of the hand. This one is fixed in the camera frame since there is no motor link between the camera and the hand. Thus, we can calculate the position of the center of the hand in the camera frame \{c\} when the robot is in its zero configuration. This offset will then be added to the command. An absence of command will not correspond to the position (0,0,0) but to the position of the end effector in camera frame so that the robot does not move. The calculation of this offset is done in the following way. The transformation matrix from the base of the camera $M_c$ and of the end effector $M_e$ in the zero configuration have been given in section 4. By multiplying these two matrices, we can obtain the transformation between the end effector and the hand $T_{ce}$. Then in the same way as we changed the reference frame from camera to base, we can pass the point (0,0,0) in the end effector frame into the camera frame.

\begin{center}
    $T_{ce} = T_{cs}T_{se} =T_{sc}^{-1}T_{se}=M_c^{-1}M_e$\\
    $p_c = T_{ce}p_e$\\
    offset $= T_{ce}\cdot[0\hspace{0.1cm}0\hspace{0.1cm}0\hspace{0.1cm}1]^T$
\end{center}
\begin{minted}[linenos=true,bgcolor=LightYellow]{Python}
    # import kinematics parameters
    from parameters import * 
    import modern_robotics as mr
    # receive angles and desired position from ros 
    p_e = np.array([0, 0, 0, 1])
    # get transformation matrix and change the position
    t_ce = np.dot(np.linalg.inv(m_c),m_e)
    translation = np.dot(t,p_e)[:3]
\end{minted}

\subsection{Open loop}

In this section, we only present the operation and results of the open loop using the tools explained above. The implementation of each block as well as the information exchanges are done with the help of ROS. Everything is detailed in the dedicated part.

\bigbreak
The user sends a desired position with the joystick, a change of reference frame is performed and then the necessary angles are calculated. The diagram above explains the different blocks used and the information exchanged between them. The camera block is separate because it does not really intervene in the loop. It is just used to obtain a video return.
\begin{figure}[H]
    \centering
    
    \caption{Open loop schema}
    \label{fig:OpenLoopSchema}
\end{figure}

To check the correct operation, we have made our arm follow a random trajectory using the joystick. As we can see on figure 7.5, the robot follows well the requested trajectory along the 3 axes.
\begin{figure}[H]
    \begin{subfigure}{.5\linewidth}
        \centering
        
        \caption{X}
        \label{fig:XboxtrajX}
    \end{subfigure}%
    \begin{subfigure}{.5\linewidth}
        \centering
        
        \caption{Y}
        \label{fig:XboxtrajY}
    \end{subfigure}\\[1ex]
    \begin{subfigure}{\linewidth}
        \centering
        
        \caption{Z}
        \label{fig:XboxtrajZ}
        \end{subfigure}
        \caption{Measure in base frame for random trajectory}
        \label{fig:Xboxtraj}
\end{figure}
\FloatBarrier

\bigbreak 
After visually checking the correct operation of the control, we subjected the robot to a \gls{step}\footnote{A discontinuous function, whose value is zero until x reaches a certain value t and a given value y when x is greater than t} according to each axis of the base. Even if we control the joystick in the camera frame, it is transformed and expressed in the base frame. We will see later, the corrector will be applied to this command, that's why we study the open loop in this reference frame. We measured the error, response time, and overshoot. The results are detailed below. All the results presented were obtained in simulation. We did not buy a sensor to measure the position of the real robot. We have therefore based ourselves on the simulation results and on the observations of the arm movements to validate the control.

\begin{table}[ht]
    \centering
    \begin{tabular}{|p{1cm} | p{2.3cm} | p{3.5cm} | p{2.3cm}| p{3.3cm} |} 
        \hline
        \textbf{Axis} & \textbf{Step (mm)} &\textbf{Time response (s)} & \textbf{error (mm)} & \textbf{Overshoot (mm)}\\ [0.3ex]
        \hline
        X & 50 & 0.24 & 1.4 & 7.6 \\ 
        \hline
        Y & 50 & 0.5 & 0.2 & 0 \\ 
        \hline
        Z & 50 & 0.2 & 0.5 & 0 \\ 
        \hline
    \end{tabular}
    \caption{Open loop result}
\end{table}
\FloatBarrier

\begin{figure}[H]
    \centering
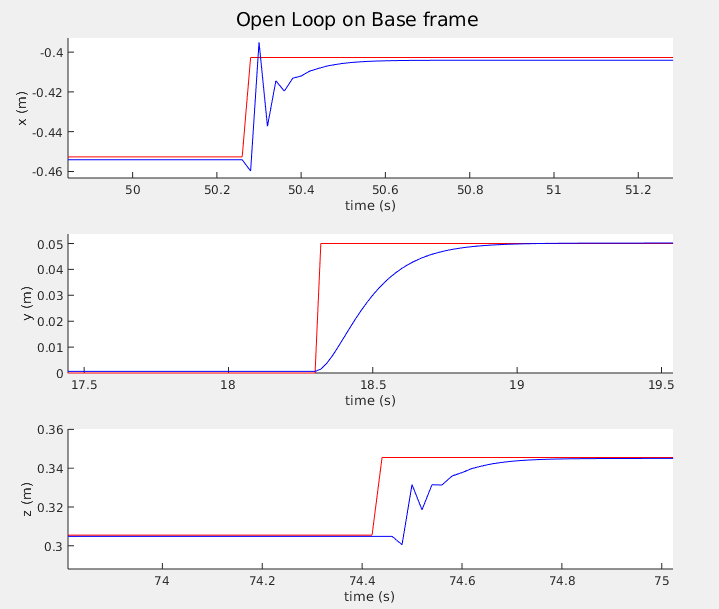
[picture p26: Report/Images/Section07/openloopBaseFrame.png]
    
    \caption{Open loop response in base frame for step input}
    \label{fig:OpenLoopGraph}
\end{figure}

\bigbreak
Using the joystick, the user gives an approximate position and corrects the desired position thanks to the camera feedback. As the results show, the open loop is accurate and allows to follow a position. Thus, it was not necessary to set up a closed loop on the real robot. We thus avoided buying a position sensor and saved development and delivery time.

\subsection{Closed loop}

However, we still servoed the robot in position in simulation. To stick to reality, we have modified a bit the robot in simulation compared to the reference robot used. Thus, we were closer to a real case and we were able to test a positional servoing using a proportional integral corrector. All this was done in simulation and was never tested on the real robot because we didn't have the time, we didn't have a sensor and the open loop was enough for a joystick control.
\begin{figure}[H]
    \centering
    
    \caption{Closed loop Schema}
    \label{fig:ClosedLoopSchema}
\end{figure}

For the corrector, we have chosen a proportional integral to suppress the error and the possible overshoot. For the adjustment, we did not calculate a theoretical value. We started with a value that works $k_p\less 1$ and $k_i\less 1$ to avoid that the solution diverges. Then we varied the parameters to increase the \gls{tr}\footnote{Also called setting time, it is the time required for the response curve to reach and stay within a range of a certain percentage of the final value} while avoiding oscillations and overshoot. An anti-\gls{windup}\footnote{The situation in a PID feedback controller where a large change in setpoint occurs (say a positive change) and the integral term accumulates a significant error during the rise} was also implemented at the output of the corrector to avoid that the control diverges. Everything was done using python. Even if it is faster to implement the PID using \textit{Matlab}, the deployment on ROS is longer. Thus, python allowed us to test different values for the corrector parameters more quickly. Finally, we subjected the arm to the same step as for the open loop and we obtained the results listed in the table and figure below.
\begin{table}[ht]
    \centering
    \begin{tabular}{|p{1cm} | p{2.3cm} | p{3.5cm} | p{2.3cm}| p{3.3cm} |} 
        \hline
        \textbf{Axis} & \textbf{Step (mm)} &\textbf{Time response (s)} & \textbf{error (mm)} & \textbf{Overshoot (mm)}\\ [0.3ex]
        \hline
        X & 50 & 1.3 & 0 & 0 \\ 
        \hline
        Y & 50 & 1.2 & 0 & 0 \\ 
        \hline
        Z & 50 & 1 & 0 & 0 \\ 
        \hline
    \end{tabular}
    \caption{Closed loop result}
\end{table}
\FloatBarrier

\begin{figure}[H]
    \begin{subfigure}{.5\linewidth}
        \centering
        
        \caption{X}
        \label{fig:ClosedX}
    \end{subfigure}%
    \begin{subfigure}{.5\linewidth}
        \centering
        
        \caption{Y}
        \label{fig:ClosedY}
    \end{subfigure}\\[1ex]
    \begin{subfigure}{\linewidth}
        \centering
        
        \caption{Z}
        \label{fig:ClosedZ}
        \end{subfigure}
        \caption{Closed loop response in base frame for step input}
        \label{fig:ClosedLoopGraph}
\end{figure}
\FloatBarrier
As we only realized this part in simulation, we did not really insist on finding the best parameters to optimize the response time. The objective here was rather to set up a closed loop and to show that it works. In view of the results, we can say that it is the case and in the case where we would like to set up a corrector on the real robot, it will be enough to spend time to find the good parameters.

\bigbreak
Finally, we have also studied the behavior of the arm when we control it with the Xbox controller in the camera's frame. We can see that the error when we stop moving the joystick is zero. However, since the response time is higher, the tracking is a little slower.
\begin{figure}[H]
    \begin{subfigure}{.5\linewidth}
        \centering
        
        \caption{X}
        \label{fig:XboxtrajClosedX}
    \end{subfigure}%
    \begin{subfigure}{.5\linewidth}
        \centering
        
        \caption{Y}
        \label{fig:XboxtrajClosedY}
    \end{subfigure}\\[1ex]
    \begin{subfigure}{\linewidth}
        \centering
        
        \caption{Z}
        \label{fig:XboxtrajClosedZ}
        \end{subfigure}
        \caption{Measure in base frame for random trajectory with closed loop}
        \label{fig:XboxtrajClosed}
\end{figure}
\FloatBarrier

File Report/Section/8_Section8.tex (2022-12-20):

\section{Vision Controle}\insertloftspace
\setcounter{figure}{0}\setcounter{table}{0}

The joystick was an explicit request from our client that he wanted us to implement. However, he wanted to relocate the workforce from the United States to Asian countries such as the Philippines. We, therefore, warned him about possible problems, especially the latency time for such a system. Indeed, the distance between Manila (the capital of the Philippines) and Los Angeles is 11,759 km. Assuming that we have a cable connecting them, which is very unlikely, the information can travel at the speed of light. A command will therefore take $\displaystyle{\frac{11759}{3.10^5}=0.04s}$. The duration between the sending of a command and the video return would be 0.08s which is considerable and would make the operation very complicated.

\bigbreak
We then looked for solutions that did not involve artificial intelligence to address this problem. However, since we still had to develop a solution using a joystick, we ran out of time. It is nevertheless a promising solution. To implement these solutions, we used the python openCV library\cite{opencvPython}. We trained ourself thanks to a python book and youtube channels.

\subsection{3D position}

Our first one consisted in making the user select the desired tomato and then estimating its 3D position using a camera. We kept the user without the need to send the order live. 

\bigbreak
The depth cameras being relatively expensive, we decided to buy only a stereo camera and to build a software able to determine the depth. All this process is done in the camera frame. It is a camera with two lenses that can retrieve two synchronized images.

\bigbreak
Using the youtube channel and the GitHub page of \textit{Nicolai Nielsen}, we calibrated the lenses to standardize the images received. Once this was done, we were able to calculate the \gls{disparity}\footnote{The apparent motion of objects between a pair of stereo images}. OpenCv has a class that allows to perform such a calcul for a calibrated \gls{sc}\footnote{A camera with two or more lenses with a separate image sensor or film frame for each lens}. Some parameters needed to be tune, and we did it thanks to sidebar until we considered we obtained the best disparity image. The code can be found on appendix \ref{disparityCode}.
\begin{figure}[H]
    \begin{subfigure}{.5\linewidth}
        \centering
        
        \caption{Disparity}
        \label{fig:disparity}
    \end{subfigure}%
    \begin{subfigure}{.5\linewidth}
        \centering
        
        \caption{Camera view}
        \label{fig:Stereoview}
    \end{subfigure}\\[1ex]
    \caption{Stereo camera image}
    \label{fig:Sci}
\end{figure}
\FloatBarrier

The figure below shows an image and its disparity. You can see that the tomato stands out a little, in a white mass. We can also note that the farther the elements on the image are, the darker they appear on the disparity image. There is indeed a correlation between disparity and distance. These are inversely proportional. To find the coefficient, we then took photos of an object at different distances known then we calculated the disparity. We then obtain the curves below which give the relationship between depth and disparity.
\begin{figure}[H]
    \centering
    
    \caption{Disparity depth relation}
    \label{fig:DisparityDepth}
\end{figure}
\FloatBarrier

Similarly, there is a link between depth and size of a pixel. Indeed, the closer an image will be, the more it will take a large place in the image. Once we were able to obtain the distance along the z axis, we wanted to calculate the position in x,y. We then sought the relationship in depth and size of a pixel. We have measured the size in pixel of the same object of known size for different depths and then we have drawn the curve. A polynomial of degree 3 seems to stick to the curve on the desired interval (10-40cm).
\begin{figure}[H]
    \centering
    
    \caption{Depth pixel size relation}
    \label{fig:DepthPixel}
\end{figure}
\FloatBarrier

The center of the image corresponds to the position (0,0). The user clicks on the center of the tomato, to get the central pixel. Using the first relation we are able to provide the distance to the camera. Then we calculate the pixel distance between the center and this point and with the second relation we calculate the position in m. We then obtain the 3D position of the center of the tomato.  We then calculate the position in the base frame and the inverse kinematics as shown in the diagram below.
\begin{figure}[H]
    \centering
    
    \caption{3D position schema}
    \label{fig:PositionSchema}
\end{figure}
\FloatBarrier

\bigbreak
Unfortunately, our solution was not precise enough. Setting up the disparity calculation with openCV would have required more time and for the same tomato, we could vary by several centimeters.

\subsection{Tracking}

The second idea consisted in object tracking. As in the previous solution, the user selects the tomato and a software developed with openCV allows to track it.
\begin{figure}[H]
    \begin{subfigure}{\linewidth}
        \centering
        
        \caption{Camera view}
        \label{fig:View}
    \end{subfigure}\\[1ex]
    \begin{subfigure}{.5\linewidth}
        \centering
        
        \caption{no tracking}
        \label{fig:notracking}
    \end{subfigure}%
    \begin{subfigure}{.5\linewidth}
        \centering
        
        \caption{tracking}
        \label{fig:tracking}
    \end{subfigure}\\[1ex]
    \caption{Computer tracking view}
    \label{fig:trackingView}
\end{figure}
\FloatBarrier

Once the tomato has been selected, a filter is applied to our image: only elements similar to the one chosen are kept. We can see that the chair in front of the camera disappears when the tracking is activated. Visually, a square highlighting the selected tomato appears on the image too.

\bigbreak
To transform this into a command, the green dot on the image in the center of the met corresponds to the lens. We must therefore center the tomato on this point. To do this, we calculate the distance in pixels between the two and we apply a command proportional to this distance on the xy plane in the camera frame. Once the tomato is centered, we can move the arm to the tomato. The overall operation is summarized in the diagram below.

\begin{figure}[H]
    \centering
    
    \caption{Object tracking schema}
    \label{fig:TrackingSchema}
\end{figure}
\FloatBarrier

Two problems then arose for us. First, our tracking system was still relatively sensitive and the arm had to move slowly at the risk of losing the tracking. Finally, we had not yet solved the question of how to stop the arm once it moves forward centered on the tomato.

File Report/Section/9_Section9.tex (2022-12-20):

\section{ROS}\insertloftspace
\setcounter{figure}{0}\setcounter{table}{0}

For our project, we used \textit{ROS}1 noetic \cite{ROS}.

\subsection{Definition}

As the name suggests, \textit{ROS} (Robot Operating System) is an operating system for robots. Like operating systems for PCs, servers, or stand-alone devices, \textit{ROS} is a complete operating system for service robotics.

\bigbreak
It is composed of a set of \gls{os}\footnote{A software with source code that anyone can inspect, modify, and enhance} allowing to develop software for robotics. \textit{ROS} is a meta operating system, something between the operating system and the middleware.

\bigbreak
\textit{ROS} is therefore positioned as a facilitator of robotics projects. Researchers or engineers in R\&D departments no longer spend time creating a new ecosystem for each new robotics project. \textit{ROS} has an accelerating effect on R\&D by reducing costs and time to market. It is therefore very interesting for the rapid development of a prototype

\bigbreak
\textbf{Master:} The master is a \textit{ROS} process that helps nodes locate each other and establish communication channels based on their publisher subscriber relationships and any services. The master also manages the parameter server. The master is typically started through the roscore command-line tool, or it is automatically started via a roslaunch call.

\bigbreak
\textbf{Topic:} A topic is a many-to-many information transport system. It is typed, it is necessary to specify which type of messages we transport and based on the system of subscription / publication 

\bigbreak
\textbf{Node:} A node is an instance of an executable; it can be linked to an engine, a sensor, or purely software. A node can post messages to a topic or subscribe to messages on a topic. They are independent processes, the crash of a node does not crash the whole \textit{ROS} (Notion of micro-kernel on which \textit{ROS} is based)

\bigbreak
\textbf{Launch file:} Launch files are very common in \textit{ROS} to both users and developers. They provide a convenient way to start up multiple nodes and a master, as well as other initialization requirements such as setting parameters.

\bigbreak
\textbf{Package:} A collection of source code, configuration files, and other resources that implements functionality in \textit{ROS}. By dividing related functionality into packages, it can be shared with others and reused across projects. All packages must have a package.xml file defining their manifest.

\bigbreak
\textbf{Workspace:} A workspace is a folder where you modify, build, and install packages.

\subsection{Training}

Following the advice of our consultant, we quickly understood the advantage of using \textit{ROS}. For that, the members of the automatic pole followed training to understand how to use it, understand the principle, the functioning, and the possible applications. Fortunately, the site offers many tutorials to learn through practice. This training was necessary and should be done as soon as possible to become familiar with totally foreign tools. We did everything using python because we had developed everything with it. 

\bigbreak
This training on \textit{ROS} is over. We knew how to create a workspace, packages, and nodes. We also decided to link \textit{Matlab} and \textit{ROS} to accelerate the development. So we followed the tutorials proposed by \textit{Matlab}\cite{MatlabROS} for the use of \textit{ROS} with \textit{Simulink} and the development of a package from the model \textit{Simulink}. This allowed us to accelerate the tests but especially the handling of \textit{ROS} because the commands were relatively automated by \textit{Matlab}. However, we were less free for the package creation. Indeed, once the model is generated, it is difficult to directly modify the package code. You have to go back to the \textit{Simulink} model and regenerate the package. Once we understood how python packages work, we limited the export of \textit{Simulink} to packages to use more python nodes which are more easily and faster to modify. We still continued to use the connection between \textit{ROS} and \textit{Matlab} for testing.

\subsection{Packages}
For this project, we decided to separate the tools into categories. Four packages have been created and one is from an existing \textit{ROS} package.
\begin{itemize}
    \item \textbf{arm}: It contains all the nodes concerning the arm (forward kinematics, change the frame, joystick conversion). It also contains all the information about the arm (kinematics parameters, rviz file, gazebo file, stl file) allowing the simulation with \textit{ROS} only.
    \item \textbf{inverse kinematics}: The inverse kinematics having been generated from \textit{Simulink}, constitutes a separate package containing only the inverse kinematics node.
    \item  \textbf{motors}: It contains all the codes related to the motors. The node listens to the instructions and sends them to the engines.
    \item  \textbf{camera}: It contains all nodes related to the camera (webcam display, object tracking, object detection)
    \item  \textbf{joy}: It allows us to get Xbox controller data.
\end{itemize}

\subsection{Topics}
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

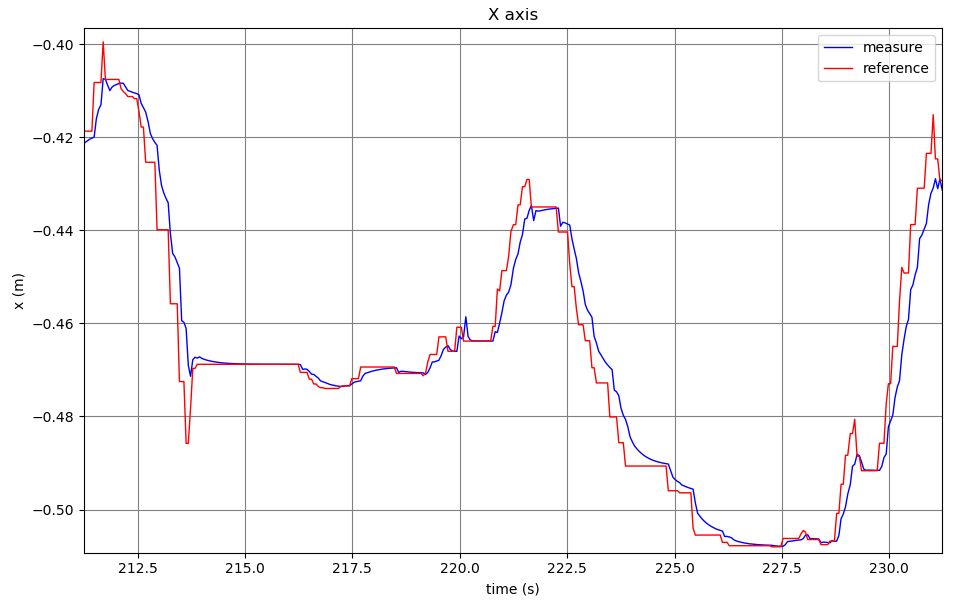
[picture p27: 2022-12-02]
Report/Images/Section07/xbox_closed_x.png

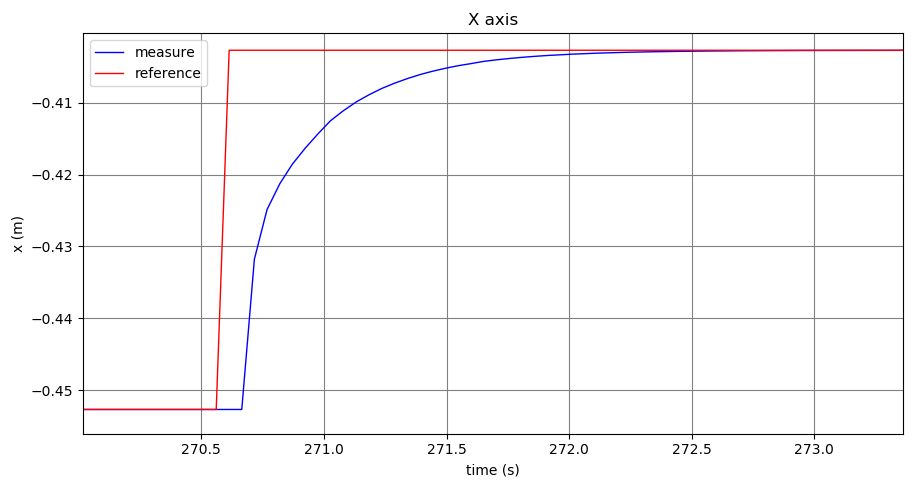
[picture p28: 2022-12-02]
Report/Images/Section07/closedloop_x.png

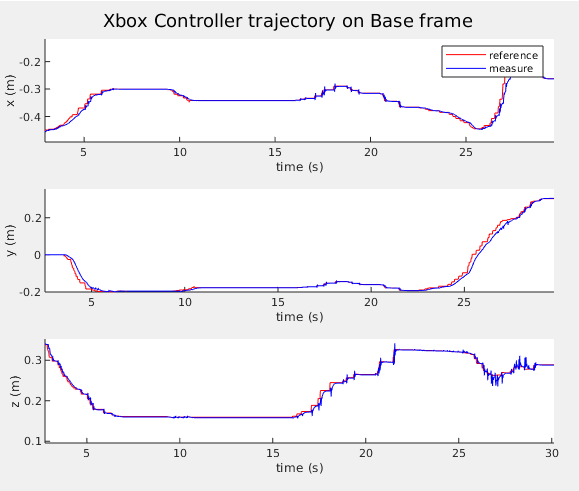
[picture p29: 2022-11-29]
Report/Images/Section07/Xbox_Controller_Trajectory.png

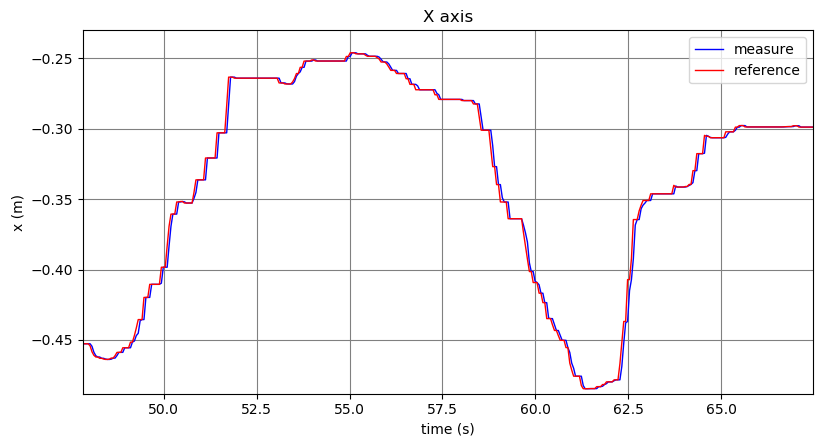
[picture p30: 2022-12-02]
Report/Images/Section07/xbox_x.png

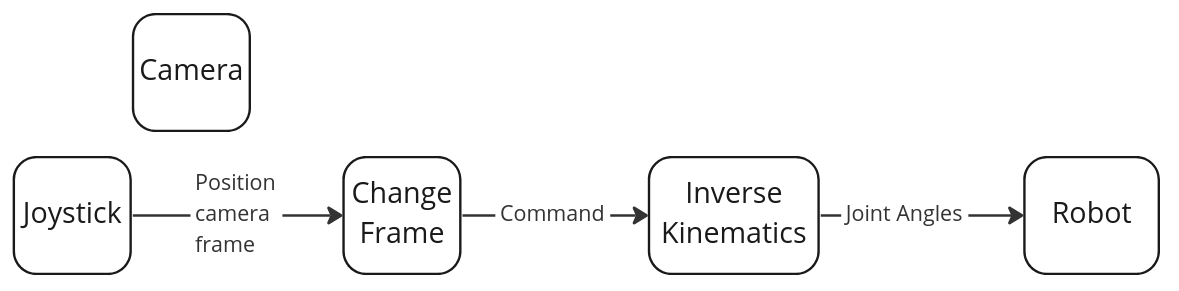
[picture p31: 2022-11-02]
Report/Images/Section07/openloop_joystick.png

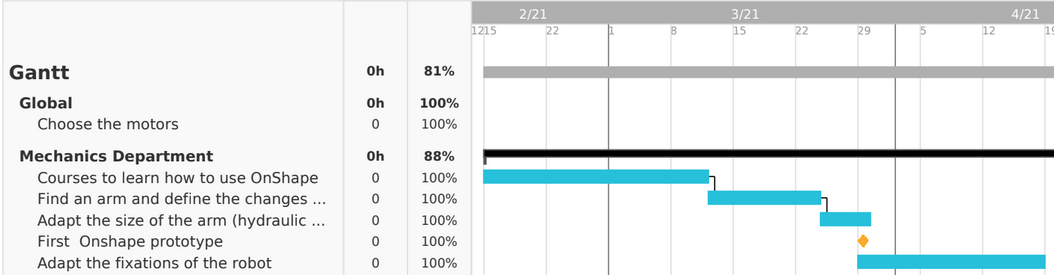
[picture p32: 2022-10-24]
Report/Images/Section02/gantt.png

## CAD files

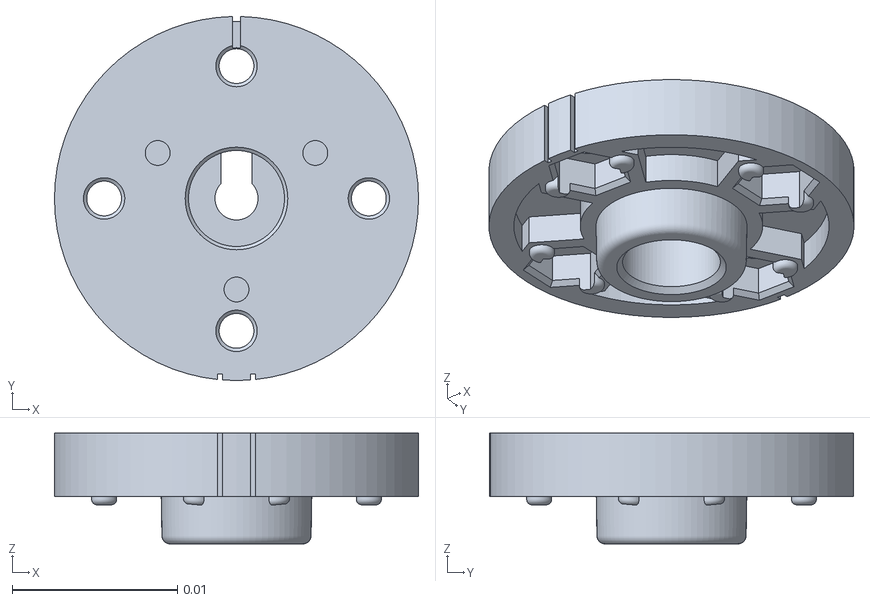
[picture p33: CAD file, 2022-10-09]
Hardware/stl/horn^horn_assembly_ax-18a.stl
0.022 x 0.022 x 0.0067

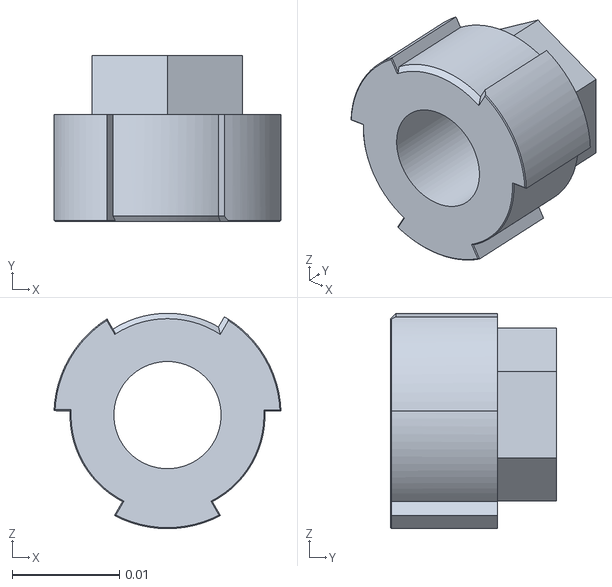
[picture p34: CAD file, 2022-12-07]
Hardware/stl/cover_rod.stl
0.0212 x 0.0155 x 0.0201

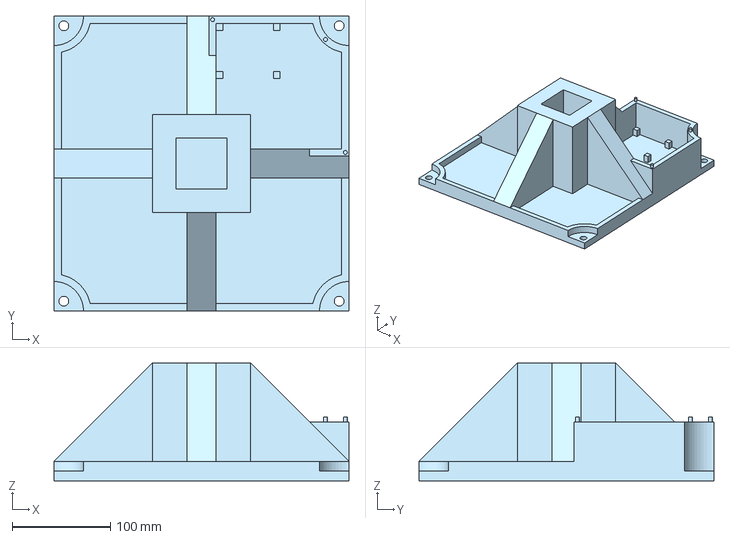
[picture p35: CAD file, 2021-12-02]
Report/Etude_Actionneurs/Matlab/Base.step
300.0 x 300.0 x 120.0 mm

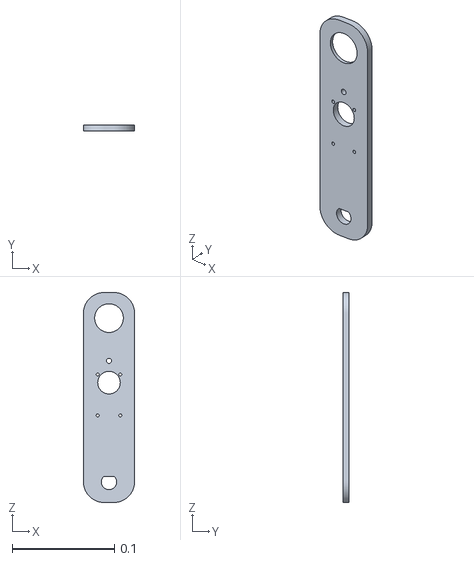
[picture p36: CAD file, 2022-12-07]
Hardware/stl/humerus.stl
0.05 x 0.006 x 0.205

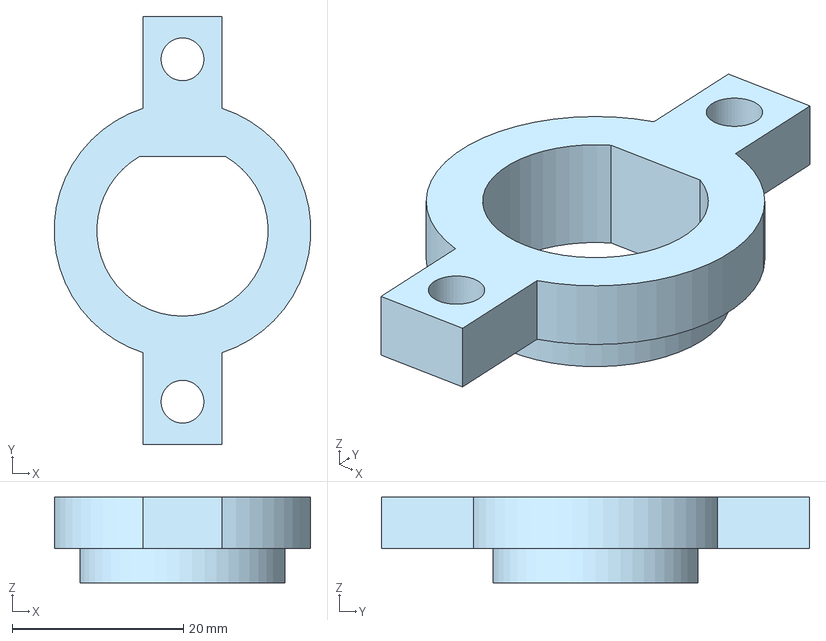
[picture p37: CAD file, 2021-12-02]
Report/Etude_Actionneurs/Matlab/Entretoise.step
29.9 x 50.0 x 10.0 mm

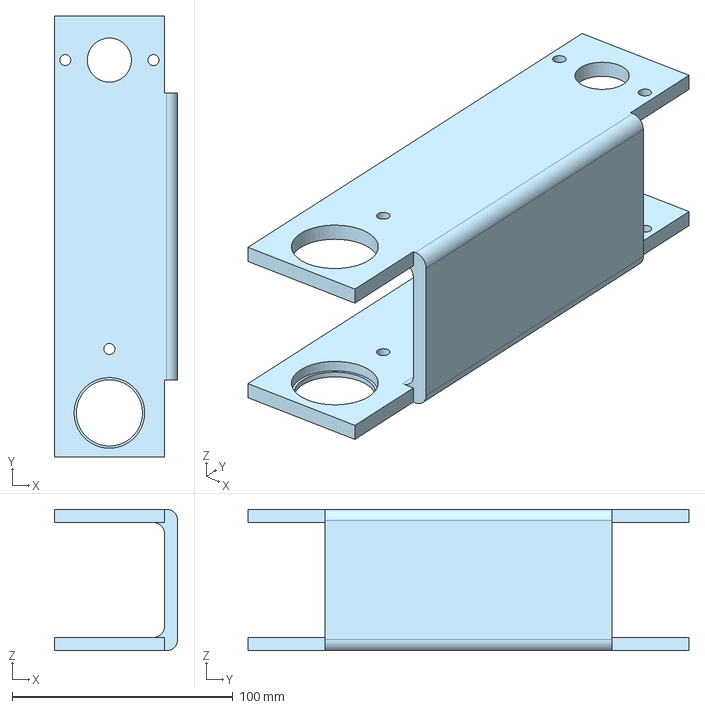
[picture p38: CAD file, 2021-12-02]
Report/Etude_Actionneurs/Matlab/Bras11.step
56.0 x 200.0 x 64.0 mm

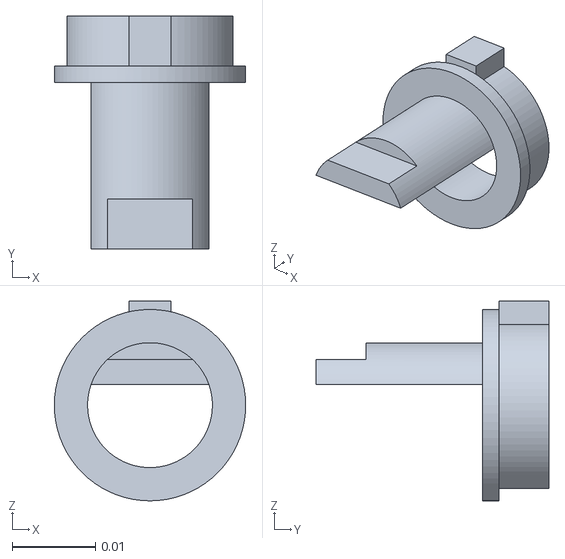
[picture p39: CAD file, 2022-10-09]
Hardware/stl/fixing_shoulder_tree.stl
0.023 x 0.028 x 0.024

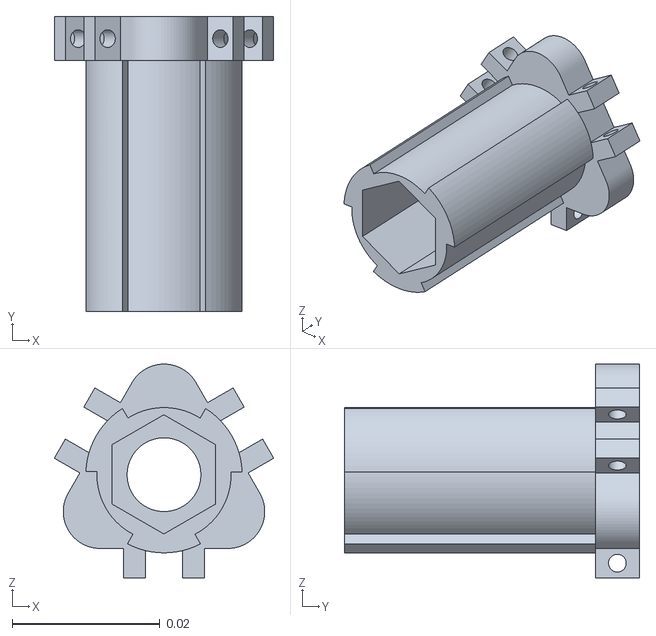
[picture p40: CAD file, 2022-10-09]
Matlab/meshes/fixing_rod.stl
0.0297 x 0.04 x 0.029

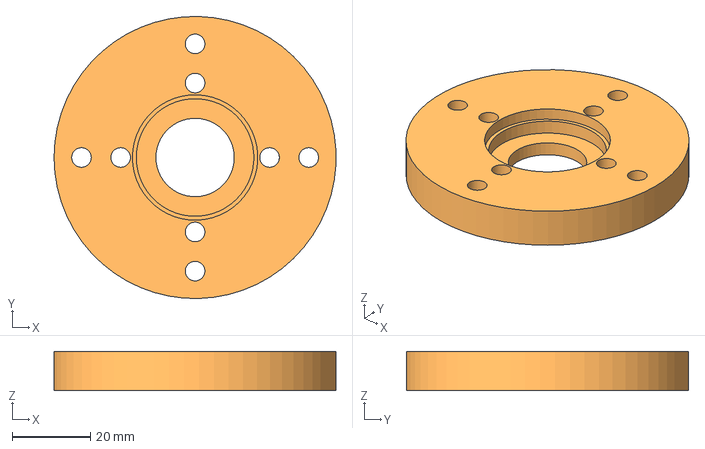
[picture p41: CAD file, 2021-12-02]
Report/Etude_Actionneurs/Matlab/Fixation moteur1.step
71.9 x 72.0 x 10.0 mm

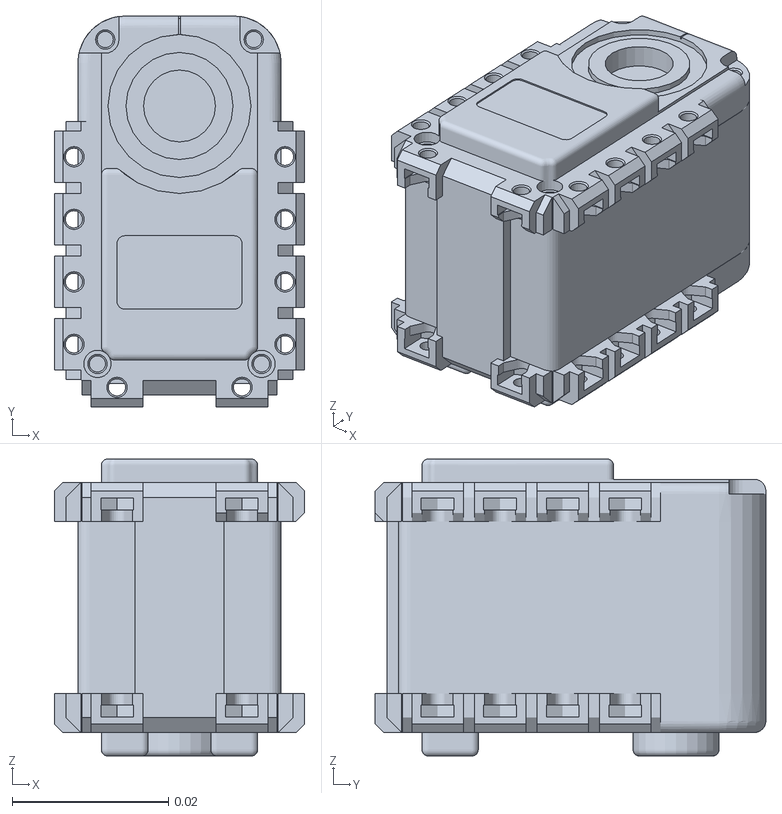
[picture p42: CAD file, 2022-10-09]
Hardware/stl/ax_12w.stl
0.032 x 0.05 x 0.038

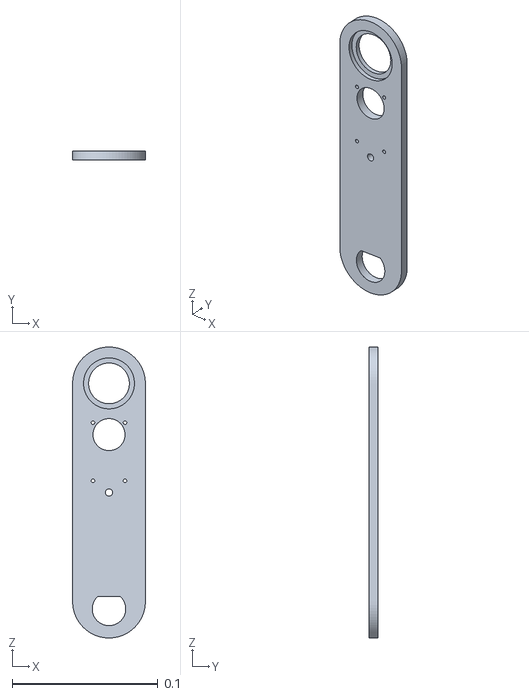
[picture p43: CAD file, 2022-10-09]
Matlab/meshes/radius.stl
0.05 x 0.006 x 0.2

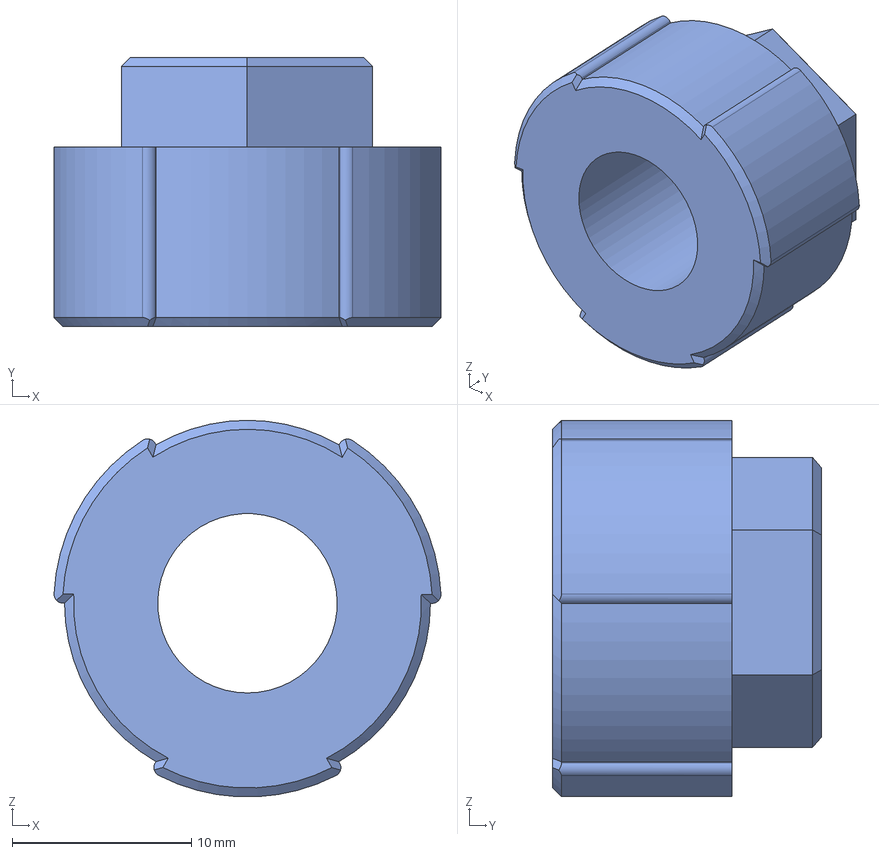
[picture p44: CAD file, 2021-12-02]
Report/Etude_Actionneurs/Matlab/Couvercle1.step
21.6 x 15.0 x 21.0 mm

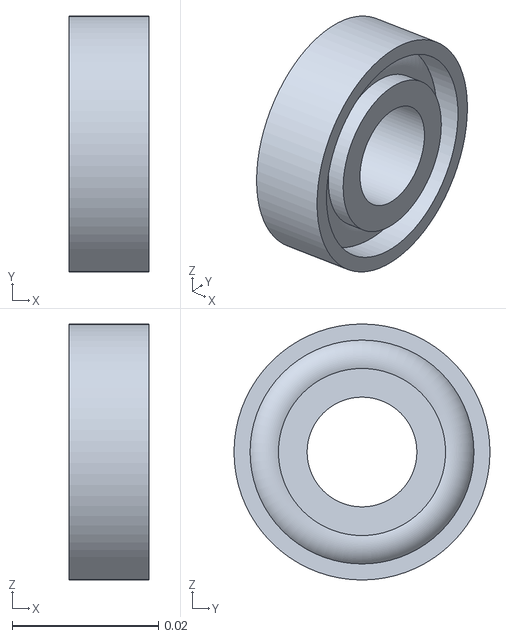
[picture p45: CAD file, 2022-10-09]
Hardware/stl/skf_7202.stl
0.011 x 0.035 x 0.035

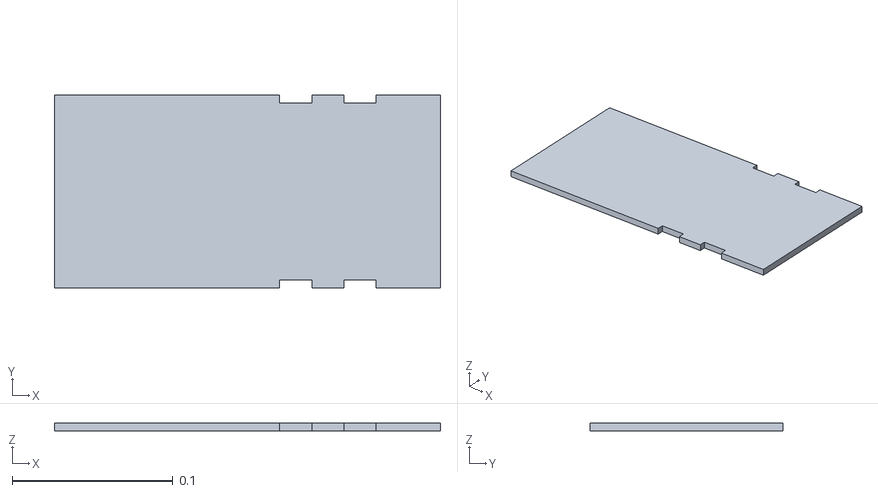
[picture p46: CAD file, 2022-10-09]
Matlab/meshes/bottom.stl
0.24 x 0.12 x 0.005

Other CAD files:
Report/Etude_Actionneurs/Matlab/Pièce intermédiaire.step
Hardware/stl/tree_elbow.stl
Hardware/stl/adapteur.stl
Hardware/stl/big_gear_elbow.stl
Hardware/stl/big_gear_pelvis.stl
Hardware/stl/big_gear_shoulder.stl
Hardware/stl/big_gear_wrist.stl
Hardware/stl/camera.stl
Hardware/stl/finger.stl
Hardware/stl/fixing_ax.stl
Hardware/stl/fixing_base_tree.stl
Hardware/stl/fixing_camera.stl
Hardware/stl/fixing_finger.stl
Hardware/stl/fixing_hand.stl
Hardware/stl/left_side.stl
Hardware/stl/motor_link_xl.stl
Hardware/stl/nut.stl
Hardware/stl/right_side.stl
Hardware/stl/skf_7208.stl
Hardware/stl/small_gear_elbow.stl
Hardware/stl/small_gear_pelvis.stl
Hardware/stl/small_gear_shoulder.stl
Hardware/stl/small_gear_wrist.stl
Hardware/stl/target.stl
Hardware/stl/top.stl
Hardware/stl/tree_base.stl
Hardware/stl/tree_shoulder.stl
Hardware/stl/tree_wrist.stl
Hardware/stl/wall_front.stl
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

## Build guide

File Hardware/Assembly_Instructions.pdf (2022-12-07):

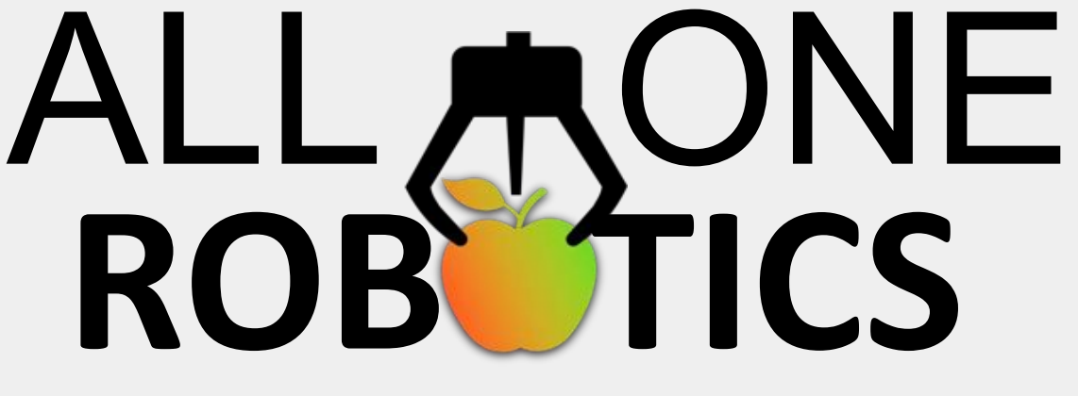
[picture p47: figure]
ROB TICS; ALL; ONE

# Assembly Instructions

# Robotic Arm

# Material

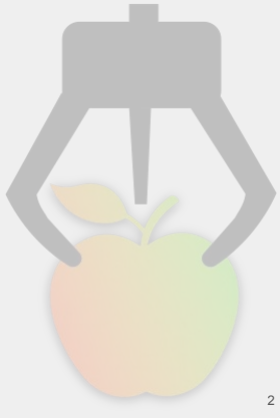
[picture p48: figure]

# Laser cutting plywood

# 3d printed PLA

# Laser cutting PVC

# steel

# Step 1

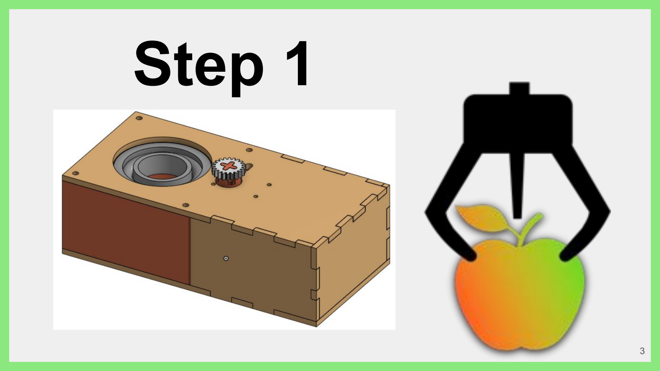
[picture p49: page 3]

# Parts

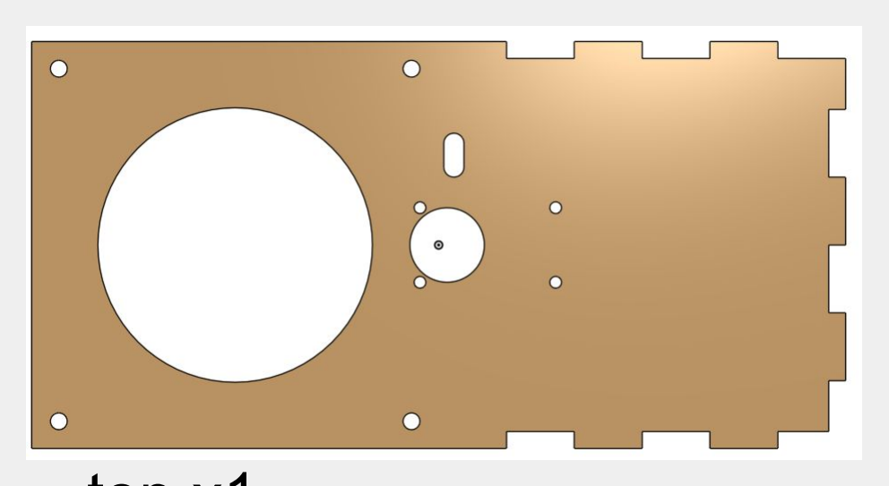
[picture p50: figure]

top x1

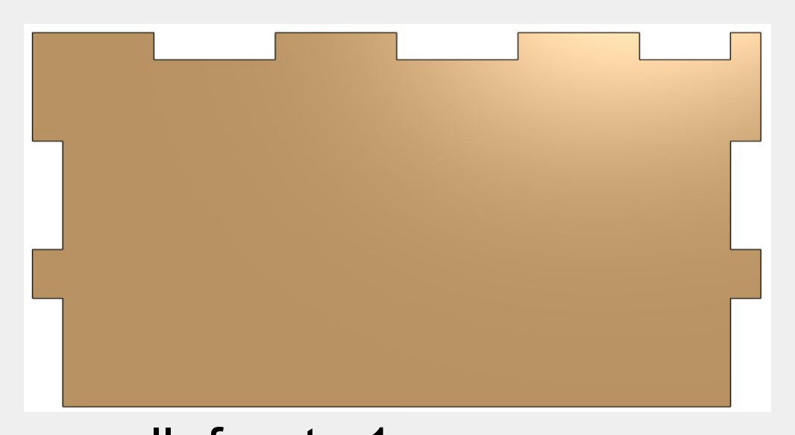
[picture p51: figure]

wall_front x1

bottom x1

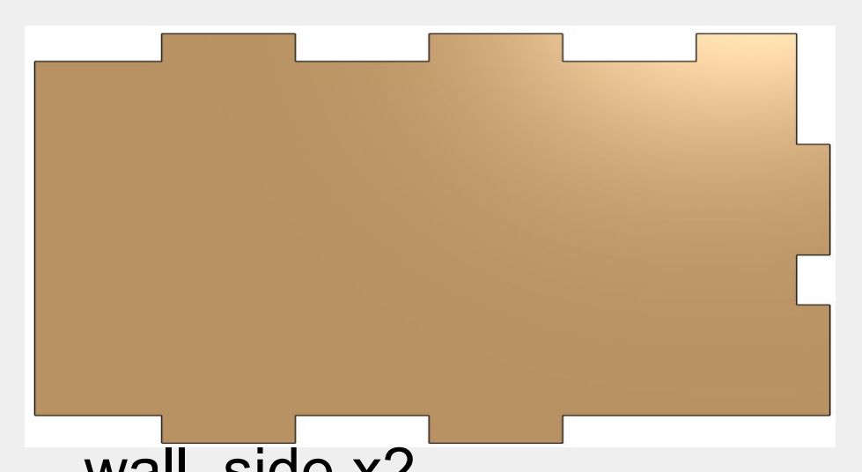
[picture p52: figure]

wall_side x2

motor_link_xl x1

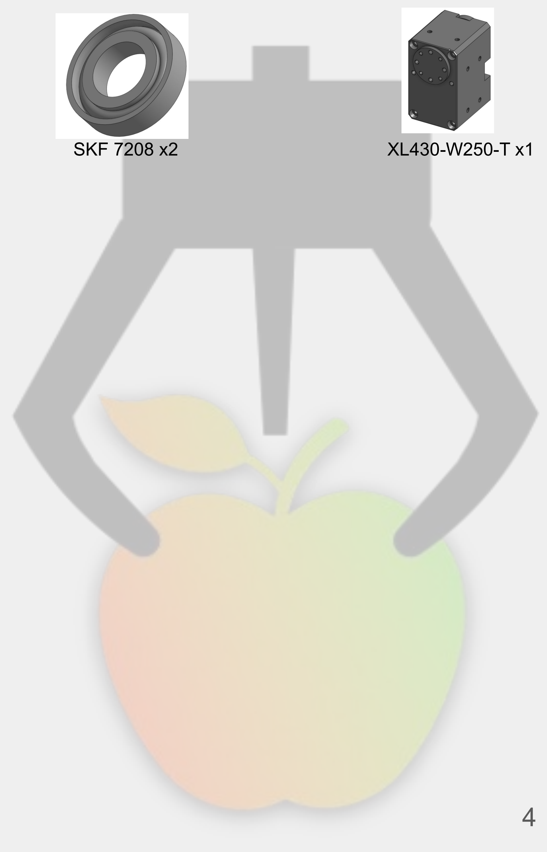
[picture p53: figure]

adapteur x1 | small_gear_pelvis (20 teeths) x1 | SKF 7208 x2 | XL430-W250-T x1

big_gear_pelvis (80 teeths) x1

tree_base x1

fixing_base_tree x1

1
4

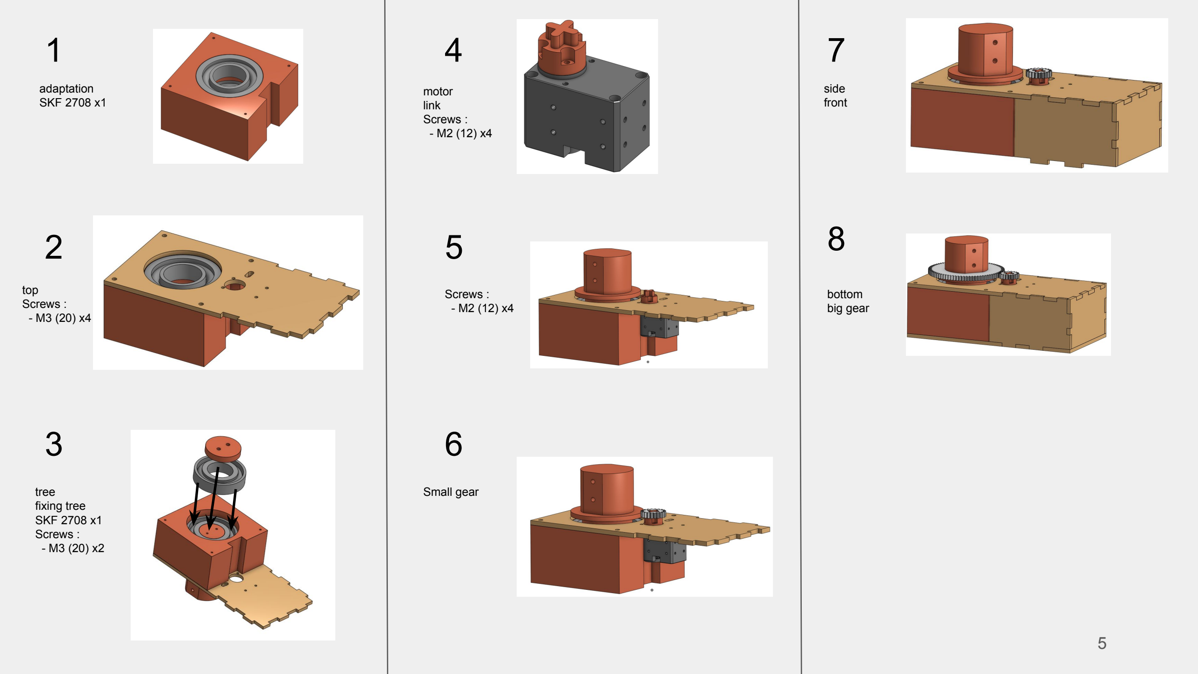
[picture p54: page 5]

5

Screws :
- M2 (12) x4

motor
link
Screws :
- M2 (12) x4

adaptation

# SKF 2708 x1 23

6

78

top
Screws :
- M3 (20) x4

tree
fixing tree
SKF 2708 x1
Screws :
- M3 (20) x2

Small gear

side
front

bottom
big gear

# Step 2

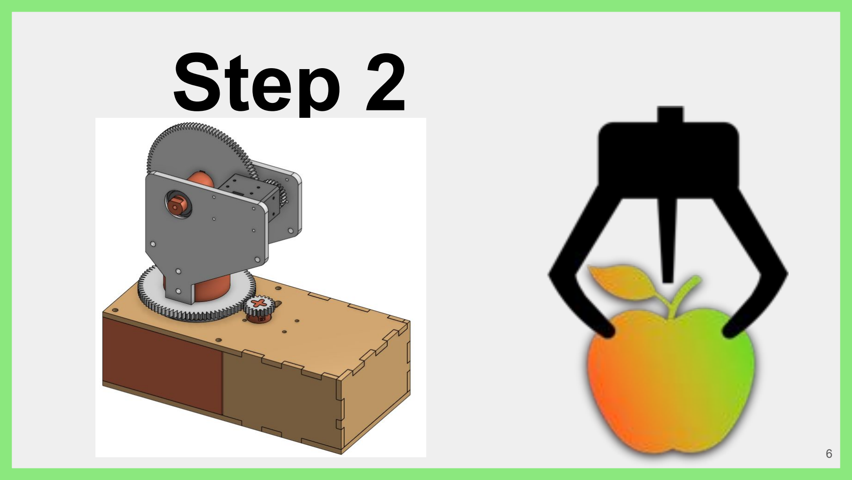
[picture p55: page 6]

# Parts

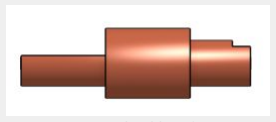
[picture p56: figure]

fixing_shoulder_tree x1

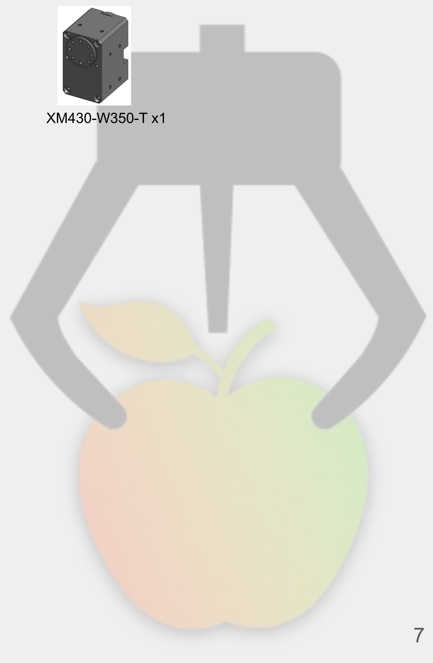
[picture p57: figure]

tree_shoulder x1 | small_gear_shoulder (25 teeths) x1 | SKF 7202 x2 | XM430-W350-T x1

big_gear_shoulder (110 teeths) x1

left_side x1

right_side x1

1

3

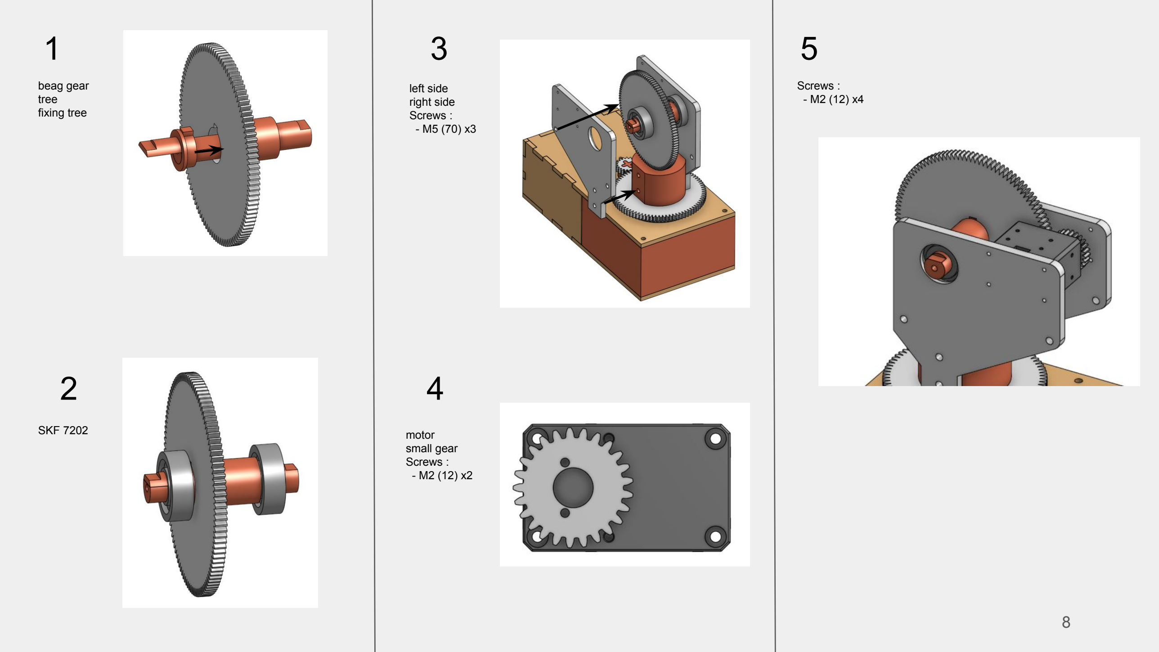
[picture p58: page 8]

left side
right side
Screws :
- M5 (70) x3

beag gear
tree

# fixing tree 2

4

5

SKF 7202 | motor
| small gear Screws :
- M2 (12) x2

Screws :
- M2 (12) x4

# Step 3

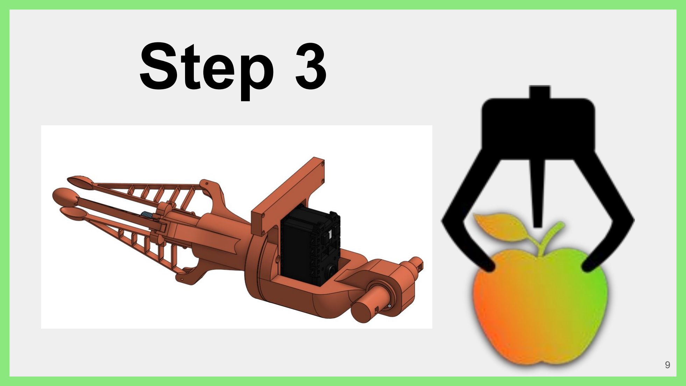
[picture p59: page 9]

# Parts

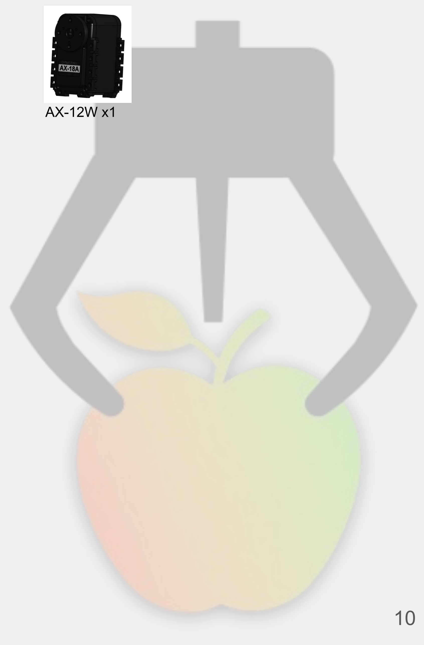
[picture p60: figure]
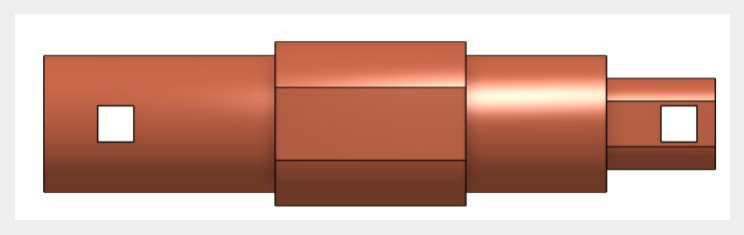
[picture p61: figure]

fixing_hand x1

tree_wrist x1 | fixing_rod x1
threaded_rod x1

cover_rod x1

finger x3

fixing_AX

fixing_camera x1

fixing_finger x1

nut x1

1
4

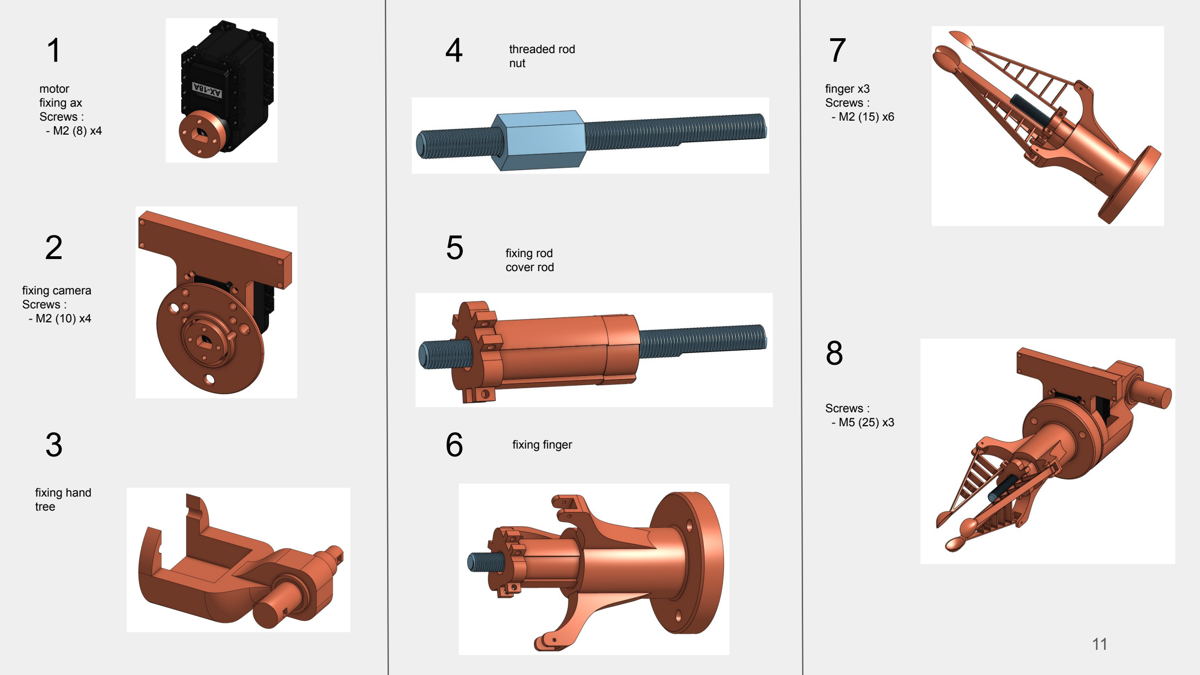
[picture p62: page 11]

5
fixing rod
cover rod

motor
fixing ax
Screws :
- M2 (8) x4 23

6

78

fixing camera
Screws :
- M2 (10) x4

fixing hand
tree

fixing finger

finger x3
Screws :
- M2 (15) x6

Screws :
- M5 (25) x3

threaded rod
nut

# Step 4

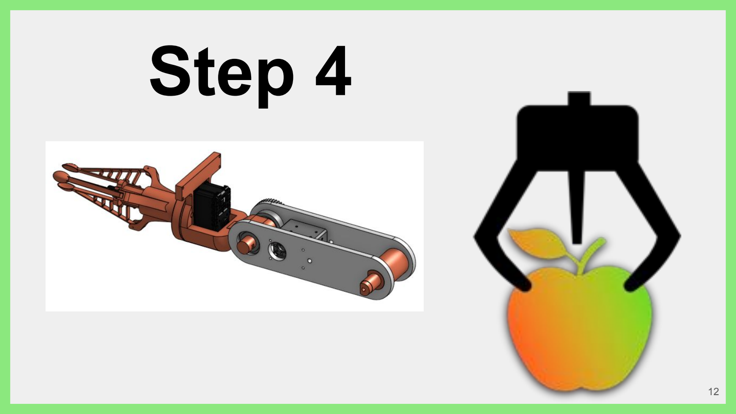
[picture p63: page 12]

# Parts

motor_link_xl x1

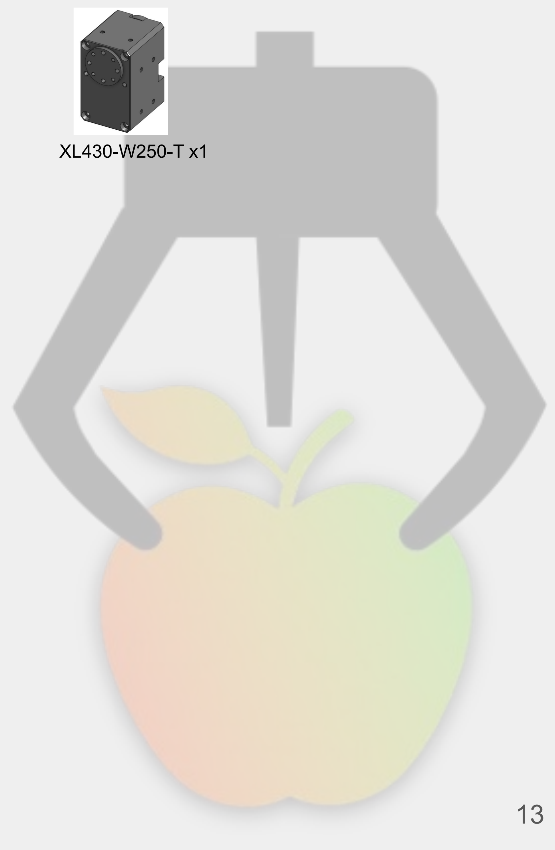
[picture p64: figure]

tree_elbow x1 | small _gear_wrist (25 teeths) x1 | SKF 7202 x2 | XL430-W250-T x1

big_gear_wrist (50 teeths) x1

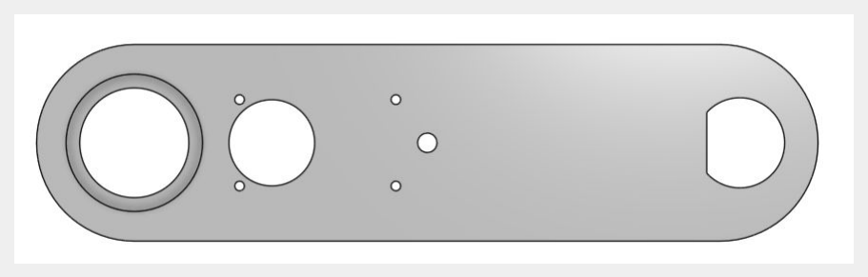
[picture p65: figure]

radius x2

1

3

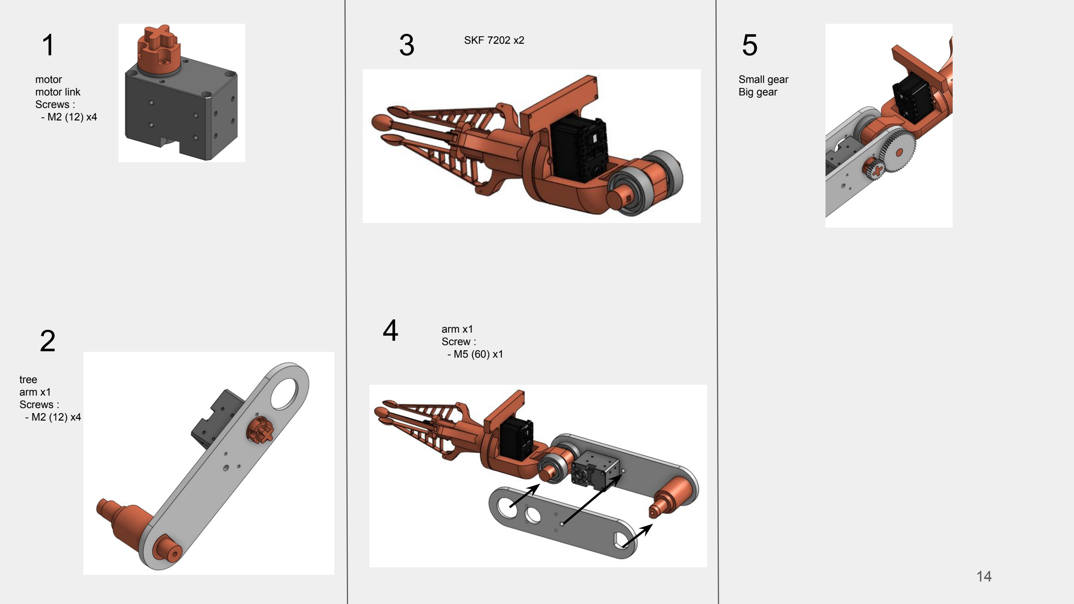
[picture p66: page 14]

SKF 7202 x2

motor
motor link
Screws :
- M2 (12) x4 2

4

5

tree
arm x1
Screws :
- M2 (12) x4

arm x1
Screw :
- M5 (60) x1

Small gear
Big gear

# Step 5

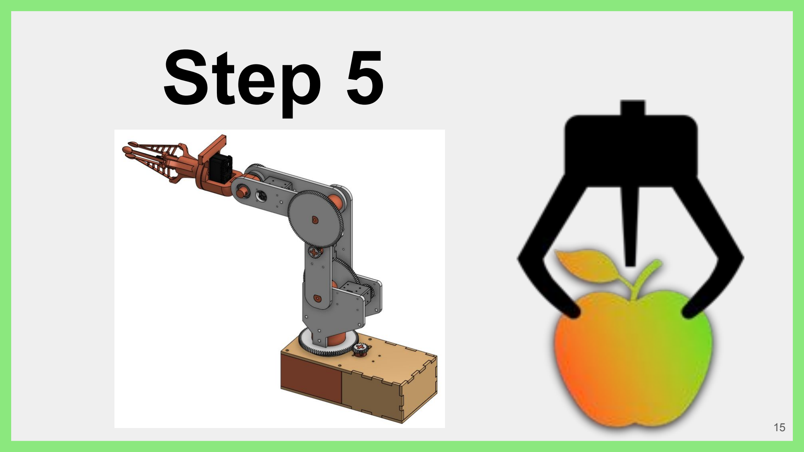
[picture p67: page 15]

# Parts

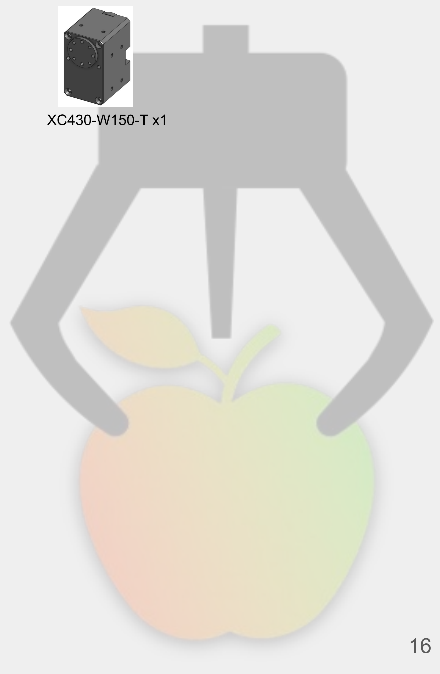
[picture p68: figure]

motor_link_xl x1 | small_gear_elbow (21 teeths) x1 | SKF 7202 x2 | XC430-W150-T x1

big_gear_elbow (105 teeths) x1

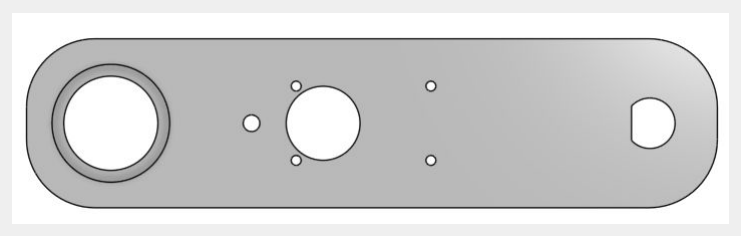
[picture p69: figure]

humerus x2

1
- M2 (12) x4 2

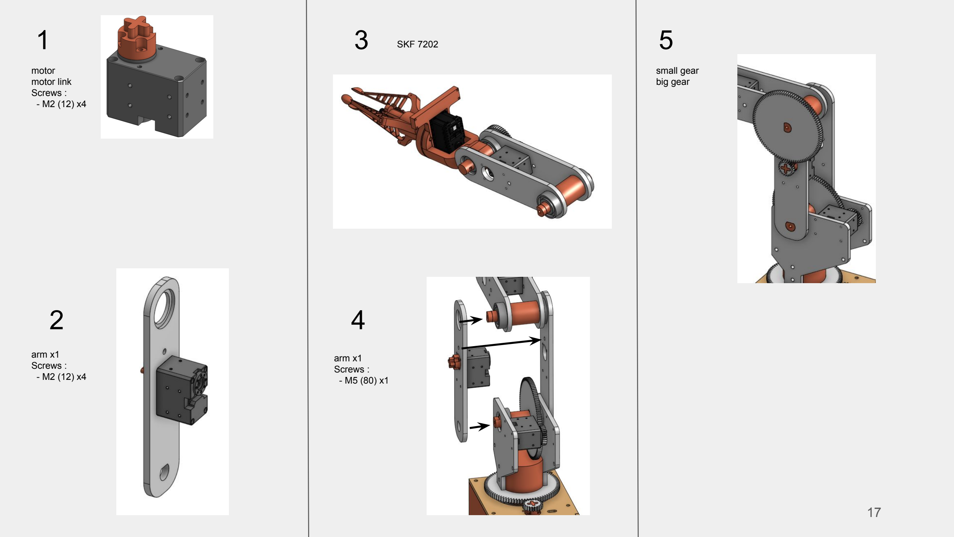
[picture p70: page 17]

3 | SKF 7202

motor
motor link
Screws :

4

5

arm x1
Screws :
- M2 (12) x4

arm x1
Screws :
- M5 (80) x1

small gear
big gear

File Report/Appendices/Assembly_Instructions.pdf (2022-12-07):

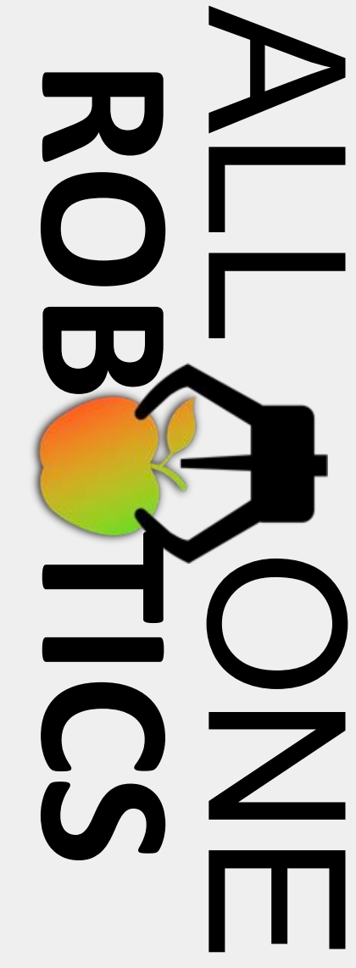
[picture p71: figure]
ROB TICS; ALL ONE

# Assembly Instructions

# Robotic Arm

# Material

# steel

# Laser cutting PVC

# 3d printed PLA

# Laser cutting plywood

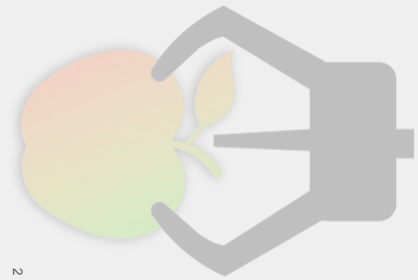
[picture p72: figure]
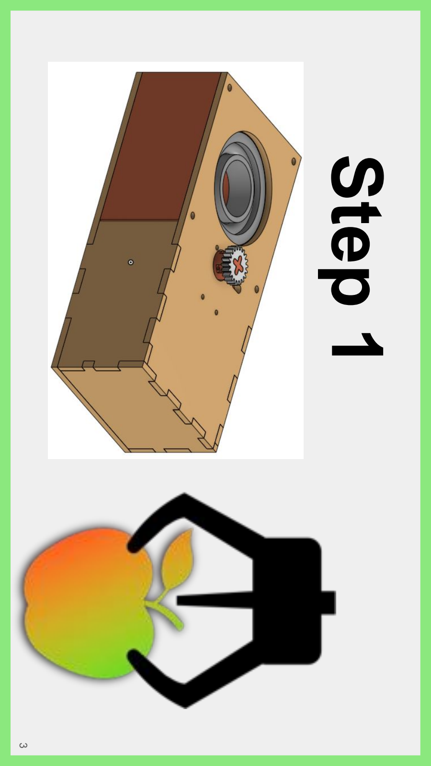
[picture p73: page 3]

# Step 1

# Parts

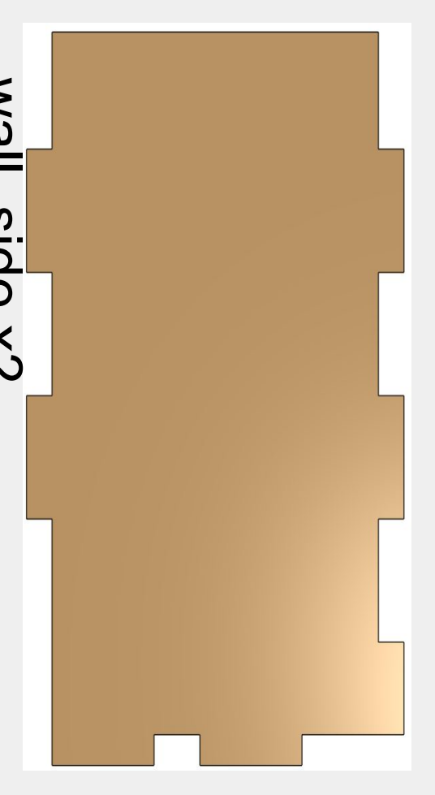
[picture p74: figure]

wall_side x2

bottom x1

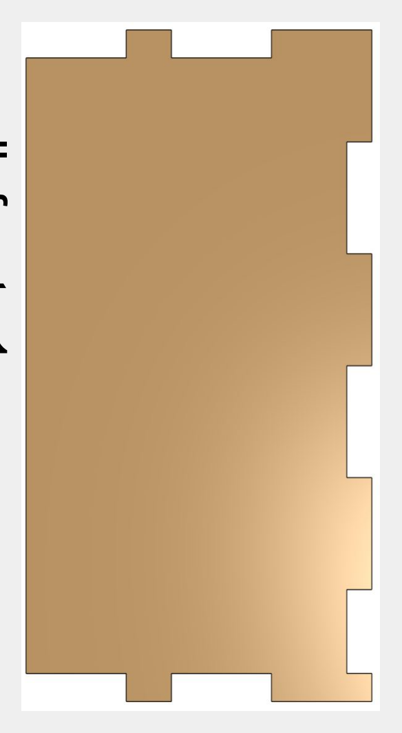
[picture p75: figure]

wall_front x1

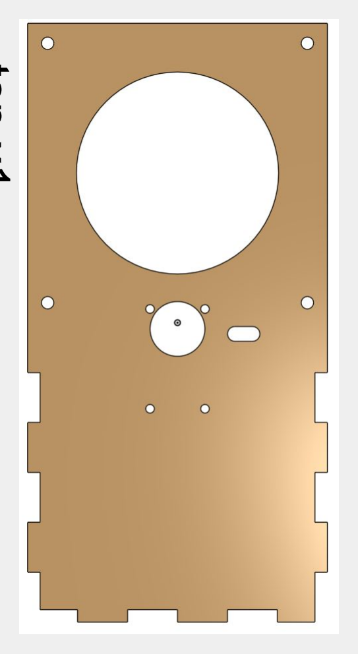
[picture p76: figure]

top x1

motor_link_xl x1
adapteur x1 small_gear_pelvis (20 teeths) x1 SKF 7208 x2 XL430-W250-T x1

big_gear_pelvis (80 teeths) x1

tree_base x1

fixing_base_tree x1

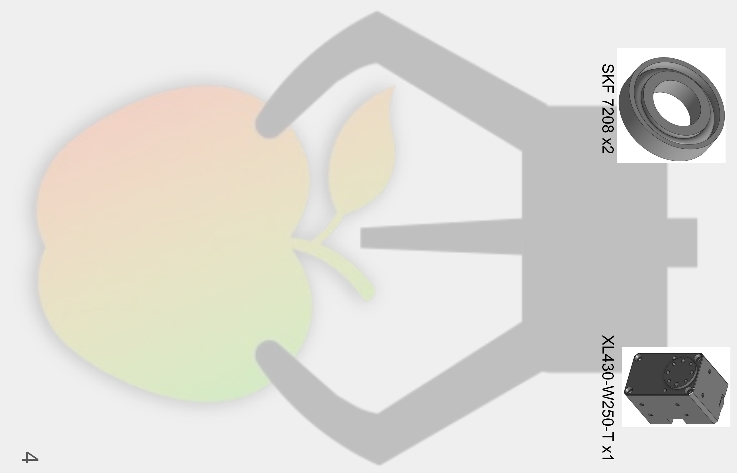
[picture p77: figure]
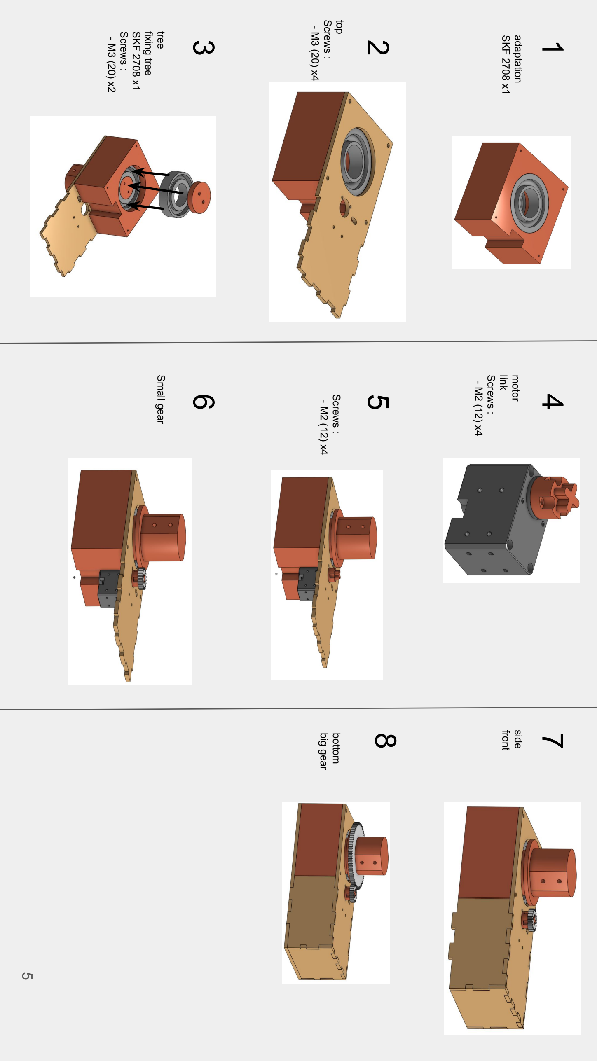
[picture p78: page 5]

54
- M2 (12) x4

Screws :

- M2 (12) x4

Screws :

link

motor

SKF 2708 x1

adaptation

6

87

- M3 (20) x4

Screws :

top

- M3 (20) x2

Screws :

SKF 2708 x1

fixing tree

tree Small gear

front

side
big gear

bottom

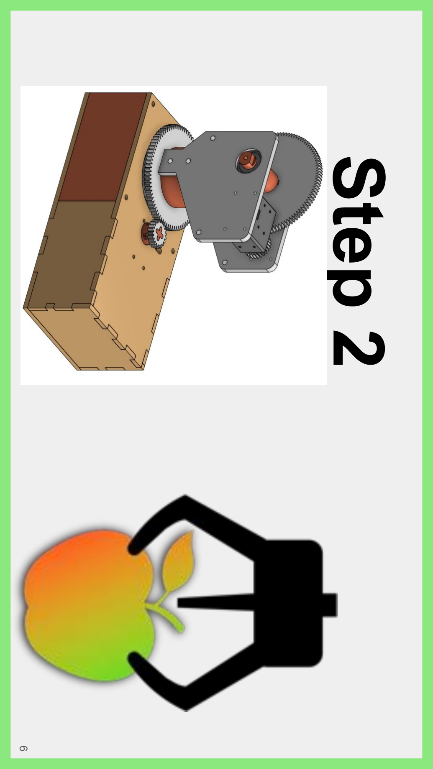
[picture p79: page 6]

# Step 2

# Parts

fixing_shoulder_tree x1

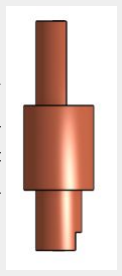
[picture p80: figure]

tree_shoulder x1 small_gear_shoulder (25 teeths) x1 SKF 7202 x2 XM430-W350-T x1

big_gear_shoulder (110 teeths) x1

left_side x1
right_side x1

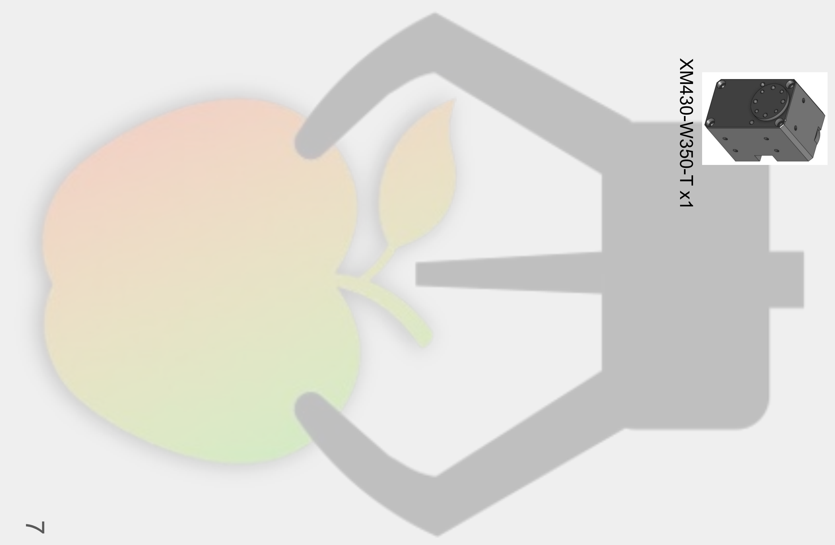
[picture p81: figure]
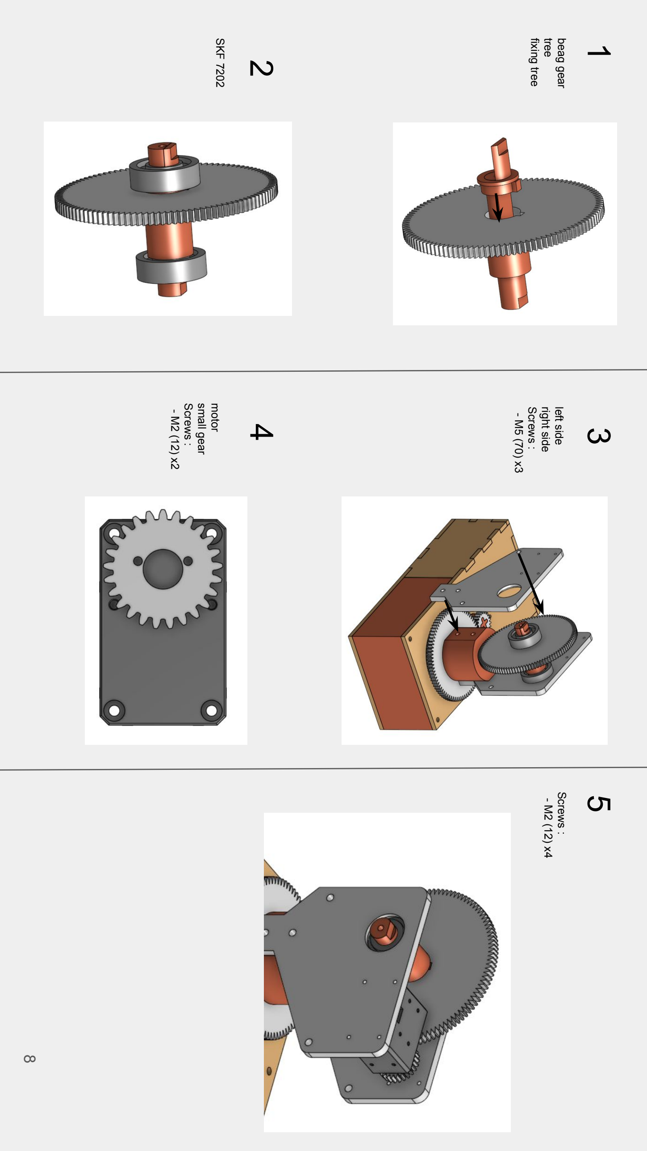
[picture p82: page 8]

3

- M5 (70) x3

Screws :

right side

left side

fixing tree

tree

beag gear 2

4

5

SKF 7202

- M2 (12) x2

Screws :

small gear

motor

- M2 (12) x4

Screws :

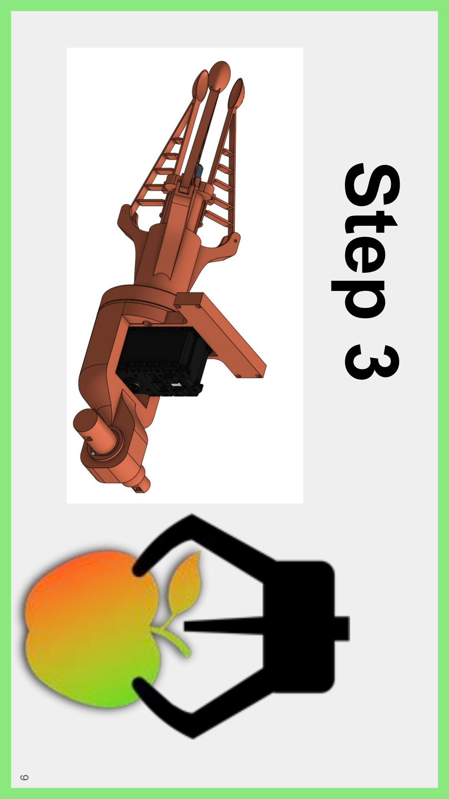
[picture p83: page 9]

# Step 3

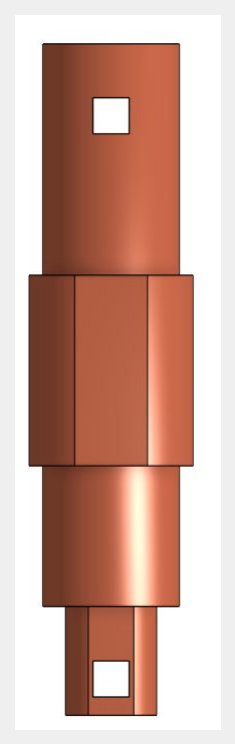
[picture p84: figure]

# Parts

fixing_hand x1
tree_wrist x1 fixing_rod x1

threaded_rod x1

cover_rod x1
fixing_AX

finger x3 fixing_camera x1 fixing_finger x1

nut x1

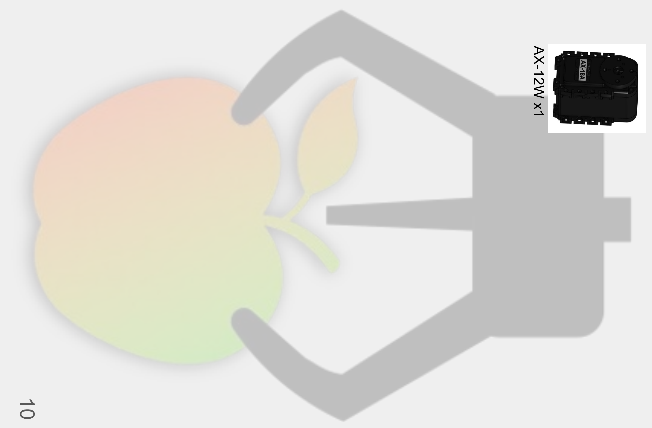
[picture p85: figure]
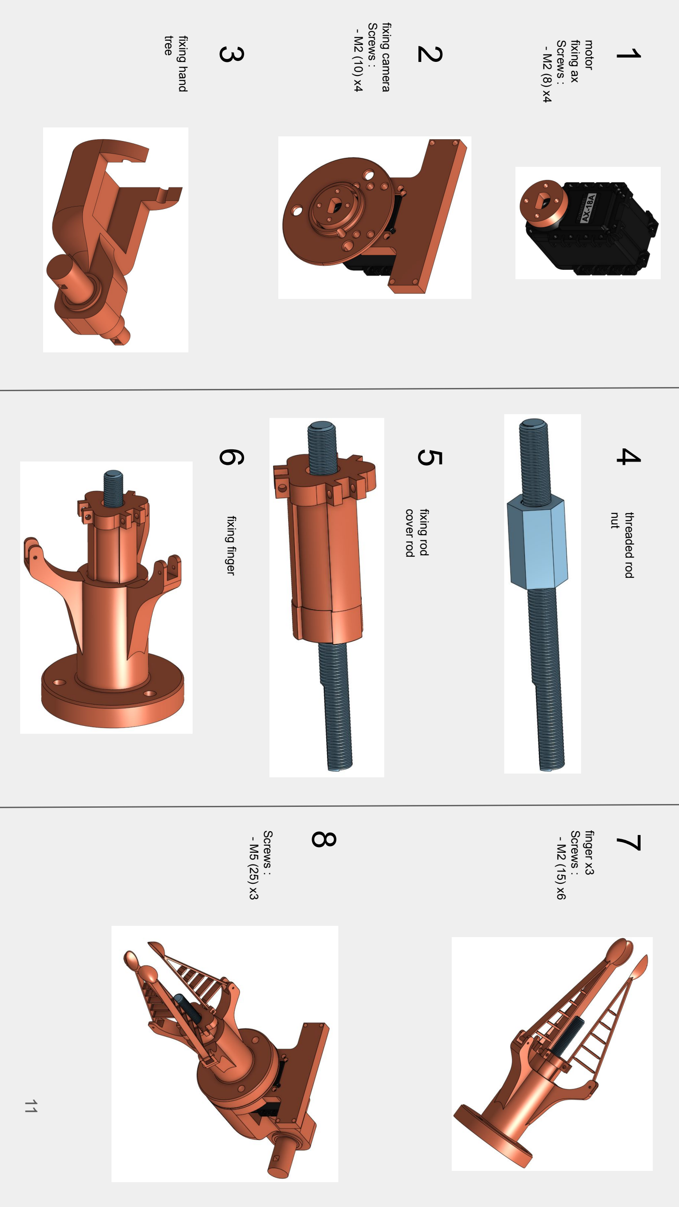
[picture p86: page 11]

11

54

cover rod

fixing rod

- M2 (8) x4

Screws :

fixing ax

motor

6

87

- M2 (10) x4

Screws :

fixing camera

tree

fixing hand

fixing finger

- M5 (25) x3

Screws :
- M2 (15) x6

Screws :

finger x3

nut

threaded rod


# Step 4

# Parts

motor_link_xl x1
tree_elbow x1 small _gear_wrist (25 teeths) x1 SKF 7202 x2 XL430-W250-T x1


big_gear_wrist (50 teeths) x1

radius x2


14

3 1

SKF 7202 x2

- M2 (12) x4

Screws :

motor link

motor

4

5

- M2 (12) x4

Screws :

arm x1

tree

- M5 (60) x1

Screw :

arm x1

Big gear

Small gear


# Step 5

# Parts

motor_link_xl x1 small_gear_elbow (21 teeths) x1 SKF 7202 x2 XC430-W150-T x1


big_gear_elbow (105 teeths) x1

humerus x2


17

# 3 1 SKF 7202

- M2 (12) x4

Screws :

motor link

motor
2 4

5

- M2 (12) x4

Screws :

arm x1

- M5 (80) x1

Screws :

arm x1

big gear

small gear

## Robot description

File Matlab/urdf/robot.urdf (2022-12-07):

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

<robot name="onshape">


    <link name="origin">
        <origin xyz="0 0 0" rpy="0 0 0" />
    </link>

    <link name="base">
        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
        <inertial>
            <origin xyz="-0.04596 -3.09902e-06 0.0414358" rpy="0 0 0"/>
            <mass value="1.26177" />
            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
        </inertial>
    </link>

    <link name="hip">
        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
        <inertial>
            <origin xyz="0.000589843 -0.0157104 -0.0737648" rpy="0 0 0"/>
            <mass value="0.468773" />
            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
        </inertial>
    </link>

    <link name="humerus">
        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
        <inertial>
            <origin xyz="-1.20261e-09 0.079896 -0.0180401" rpy="0 0 0"/>
            <mass value="0.390303" />
            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
        </inertial>
    </link>

    <link name="radius">
        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
        <inertial>
            <origin xyz="-1.50407e-09 0.0815245 -0.0176273" rpy="0 0 0"/>
            <mass value="0.380955" />
            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
        </inertial>
    </link>

    <link name="hand">
        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
        <inertial>
            <origin xyz="0.00378438 0.0815063 -0.01325" rpy="0 0 0"/>
            <mass value="0.191614" />
            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
        </inertial>
    </link>

    <link name="camera">
        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
        <inertial>
            <origin xyz="-0.003 -1.23123e-19 -0.0015" rpy="0 0 0"/>
            <mass value="0.000135" />
            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
        </inertial>
    </link>

    <joint name="camera" type="fixed">
        <origin xyz="0.0560004 0.08 -0.0105" rpy="1.5708 -1.70787e-28 1.9082e-16" />
        <parent link="hand" />
        <child link="camera" />
        <axis xyz="0 0 1"/>
        <limit effort="1" velocity="20" />
        <joint_properties friction="0.0"/>
    </joint>

    <link name="target">
        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
        <inertial>
            <origin xyz="1.35525e-20 -6.41848e-17 -0.0015" rpy="0 0 0"/>
            <mass value="3.375e-05" />
            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
        </inertial>
    </link>

    <joint name="fixed" type="fixed">
        <parent link="origin"/>
        <child link="base"/>
    </joint>

    <joint name="target" type="fixed">
        <origin xyz="0.000500416 0.23624 -0.0105" rpy="1.5708 1.5708 0" />
        <parent link="hand" />
        <child link="target" />
        <axis xyz="0 0 1"/>
        <limit effort="1" velocity="20" />
        <joint_properties friction="0.0"/>
    </joint>

    <joint name="wrist" type="revolute">
        <origin xyz="-4.77396e-15 0.155 -0.014125" rpy="2.22045e-16 -2.15076e-25 -4.74015e-14" />
        <parent link="radius" />
        <child link="hand" />
        <axis xyz="0 0 1"/>
        <limit effort="1" velocity="20" lower="0" upper="1.5708"/>
        <joint_properties friction="0.0"/>
    </joint>

    <joint name="elbow" type="revolute">
        <origin xyz="1.38778e-17 0.16 -0.042" rpy="3.14159 1.78606e-16 1.5708" />
        <parent link="humerus" />
        <child link="radius" />
        <axis xyz="0 0 1"/>
        <limit effort="1" velocity="20" lower="-1.5708" upper="1.0472"/>
        <joint_properties friction="0.0"/>
    </joint>

    <joint name="shoulder" type="revolute">
        <origin xyz="-0.018 2.08167e-17 -0.116" rpy="-1.5708 7.82376e-14 1.5708" />
        <parent link="hip" />
        <child link="humerus" />
        <axis xyz="0 0 1"/>
        <limit effort="1" velocity="20" lower="-1.5708" upper="0.698132"/>
        <joint_properties friction="0.0"/>
    </joint>

    <joint name="pelvis" type="revolute">
        <origin xyz="-0.06 6.93889e-18 0.069" rpy="3.14159 -1.19271e-28 -1.5708" />
        <parent link="base" />
        <child link="hip" />
        <axis xyz="0 0 1"/>
        <limit effort="1" velocity="20" lower="-1.5708" upper="1.5708"/>
        <joint_properties friction="0.0"/>
    </joint>


</robot>

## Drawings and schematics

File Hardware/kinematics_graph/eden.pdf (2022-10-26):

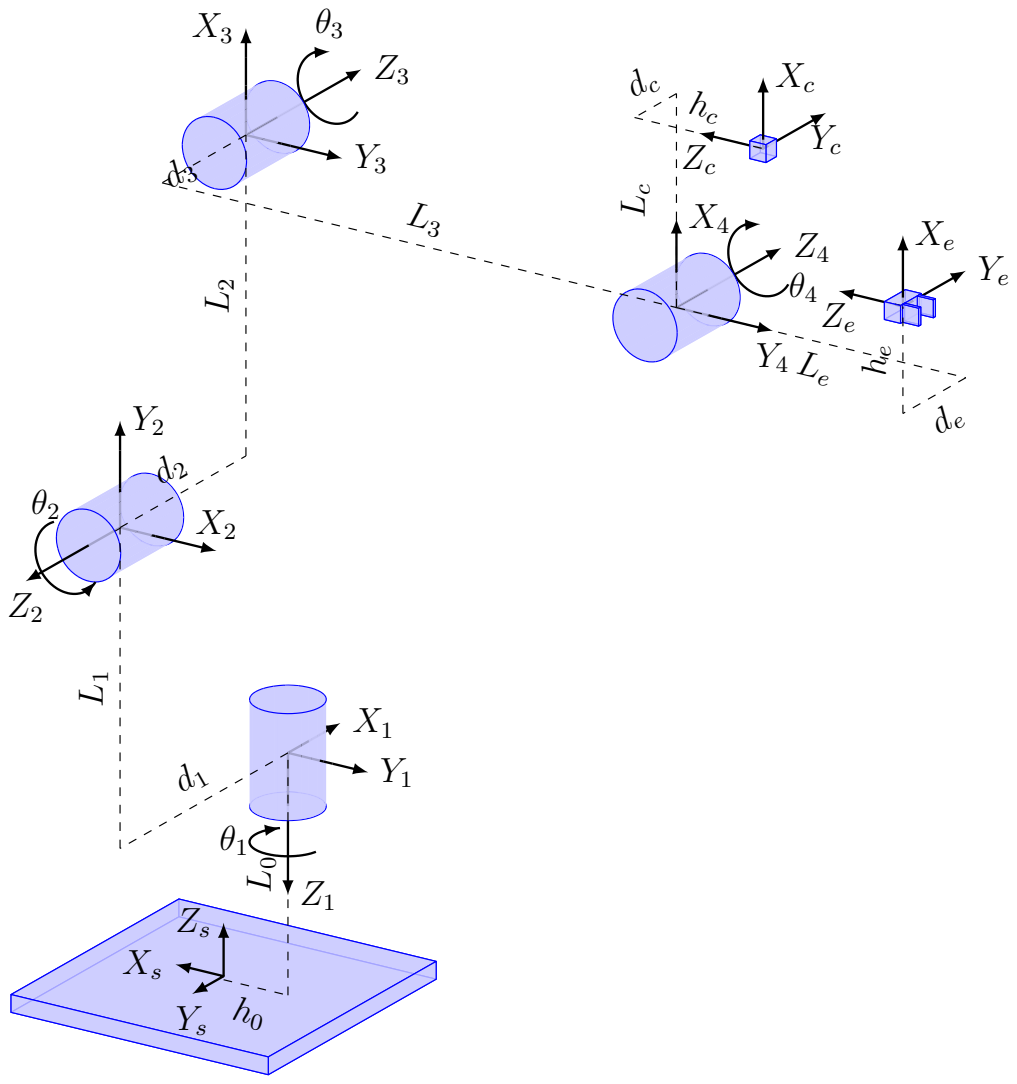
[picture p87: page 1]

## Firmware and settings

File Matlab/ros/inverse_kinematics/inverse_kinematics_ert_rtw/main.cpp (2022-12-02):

//
// File main.cpp
//
// Code generated for Simulink model 'inverse_kinematics'.
//
// Model version                  : 4.51
// Simulink Coder version         : 9.7 (R2022a) 13-Nov-2021
// C/C++ source code generated on : Wed Nov 30 11:09:31 2022
//

#include <stdio.h>
#include "rosnodeinterface.h"
#include "slros_initialize.h"

extern void slros_node_init(int argc, char** argv);
namespace ros
{
  namespace matlab
  {
    std::shared_ptr<ros::matlab::NodeInterface> gMatlabNodeIntr;
    std::shared_ptr<ros::matlab::NodeInterface> getNodeInterface()
    {
      return gMatlabNodeIntr;
    }
  }                                    //namespace matlab
}                                      //namespace ros

int main(int argc, char* argv[])
{
  // create the Node specified in Model
  slros_node_init(argc, argv);
  ros::matlab::gMatlabNodeIntr = std::make_shared<ros::matlab::NodeInterface>();
  ros::matlab::gMatlabNodeIntr->initialize(argc, argv);
  auto ret = ros::matlab::gMatlabNodeIntr->run();
  ros::matlab::gMatlabNodeIntr->terminate();
  ros::matlab::gMatlabNodeIntr.reset();
  return ret;
}

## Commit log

2022-10-05 Change frame +IK
2022-10-09 urdf python Matlab
    [adapteur.stl, arm_elbow.stl, ax_12w.stl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]
2022-10-09 Hardware part
    [adapteur.stl, arm_elbow.stl, ax_12w.stl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]
2022-10-10 ClosedLoop Matlab
    [AX_12W.step, Adaptateur Arbre 01.step, Arbre 1.step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]
2022-10-13 New urdf
    [robot.urdf]
2022-10-15 inverse kinematics correction
    [big_gear_pelvis.stl, robot.urdf, small_gear_pelvis.stl]
2022-10-16 kinematics schema
2022-10-19 Part1 project def
    [robot.urdf]
2022-10-24 Report management
    [robot.urdf]
2022-10-24 report kinematics
2022-10-26 report urdf
2022-10-26 report URDF format
2022-11-02 report ros inverse kinematics
2022-11-05 report workspace
    [workspace.csv]
2022-11-25 torque, power speed motors analysis
2022-11-27 report motors specification
2022-12-07 assembly instructions
2022-12-07 urdf correction
    [bottom.stl, cover_rod.stl, fixing_rod.stl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]
2022-12-07 rename stl
    [left_side.stl, right_side.stl, robot.urdf]
